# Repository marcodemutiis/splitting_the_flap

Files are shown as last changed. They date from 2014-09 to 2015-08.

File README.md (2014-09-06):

splitting_the_flap
==================

modular split-flap units

splitting the flap is a modular split flap display system based on Arduino. Split flap displays were invented by Solari di Udine in the 60's and used in several train stations and airports around the world. Now out of production and on the path to extinction, I have tried to be as close as possible to the original iconic design.

Project is currently at prototyping stage and files are under constant development - use at your own risk.
stage 0: https://www.youtube.com/watch?v=zjAqb3puniw

All fabrication, circuit and code files are released under MIT license.

For any question, please contact me at: me [at] marcodemutiis.com

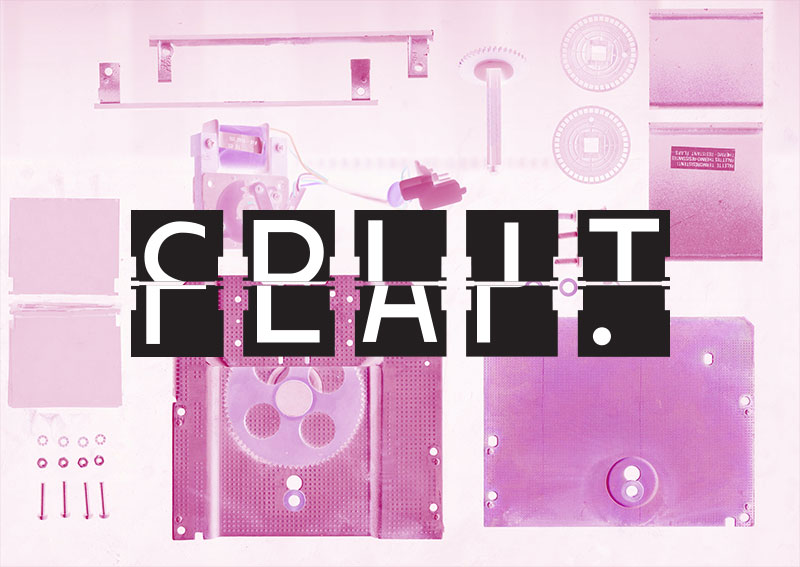
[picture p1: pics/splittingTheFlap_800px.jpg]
splitting_the_flap


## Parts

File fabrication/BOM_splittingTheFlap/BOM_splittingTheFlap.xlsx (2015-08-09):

splitting the flap
Bill of materials (per unit)
PART | NAME | quantity | link | price/unit | price/total
motor | 39步进电机驱动器 39BYG小型电机 20MM机身 0.4A 8N.CM 两相四线 | 1 | http://world.taobao.com/item/17026801379.htm?fromSite=main&spm=a1z09.2.9.60.DnxNuo&_u=91qs2dec14e4
screws | 尼龙/塑料六角螺母 塑胶螺丝螺帽 M2-2.5-3-4-5-6-8-10-12(50颗) [交易快照] 颜色分类: M2.0 白
screws | 颜色分类: M2.0 圆头十字尼龙螺丝 元机尼龙螺钉 塑料螺丝 塑胶螺丝 M2 [交易快照] 颜色分类: m2*12
nylon screws and holders |  |  | https://tengluowujin.world.tmall.com/shop/view_shop.htm?user_number_id=1099047830
acrylic 2.8mm transparent
acrylic 3mm transparent
acrylic 2mm black
acrylic 4mm transparent
EasyDriver |  | 1 | http://world.taobao.com/item/38230922222.htm?fromSite=main&spm=a1z09.2.9.46.DnxNuo&_u=91qs2dec0f0e
rj45 connector (ethernet) | RJ45插座 90度卧式 网络插座 网口母座 56-8P8C全塑 L=17.8mm [交易快照] | 1 | https://klmsm.world.tmall.com/shop/view_shop.htm?spm=a1z09.2.9.160.bYsZt7&user_number_id=1743088708
jumper wires F-F (hall sensor connectors) | 40P杜邦线 双头1P胶壳 总长21CM 12股铜丝 彩排线 40根一排 | 1 | http://world.taobao.com/item/2834445432.htm?fromSite=main&spm=a1z09.2.9.47.s9rnjw&_u=91qs2decbf6f
headers male straight
headers female straight
headers 90 degree male
PVC
PVC silkscreen | 收藏 分享复制链接 举报 透明PVC片丝印 磨砂PVC丝印 面板PVC标贴印刷 服装吊牌标签 |  | http://world.taobao.com/item/38409216170.htm?fromSite=main&spm=a1z09.2.9.230.DnxNuo&_u=91qs2dec7a66
PVC mould cutting |  |  | http://world.taobao.com/item/38409216170.htm?fromSite=main&spm=a1z09.2.9.230.DnxNuo&_u=91qs2dec7a66
acrylic lasercutting |  |  | https://item.taobao.com/item.htm?spm=a1z09.2.9.13.DnxNuo&id=20099696260&_u=91qs2dec31db
ethernet cables | AMPCOM安普康成品六类网线 纯铜CAT6扁平跳线 1/2/3/5/8/10/15米 [交易快照] 颜色分类: 2米无氧铜千兆速率) | 1 | https://ampcom.world.tmall.com/shop/view_shop.htm?spm=a1z09.2.9.183.y7qHXO&user_number_id=2024267815
hall sensors | OH090U(TT ELECTRONICS/OPTEK TECHNOLOGY)[全新原装] | 1 | http://world.taobao.com/item/42828434479.htm?fromSite=main&spm=a1z09.2.9.78.1xjDX0&_u=91qs2deca021
magnets | 稀土永磁王 钕铁硼超强磁钢 永磁铁 白板 方形强力吸铁石4*4*2MM [交易快照] | 1 | https://magpanda.world.tmall.com/shop/view_shop.htm?user_number_id=379092803
PCB print | （冲5钻优惠）3-4天发货 PCB加工 打样 双面板制作5*5 45元10片 | 1 | http://world.taobao.com/item/13063584813.htm?fromSite=main&spm=a1z09.2.9.244.DnxNuo&_u=91qs2dec15ce
resistor
Bill of material (per arduino mega shield)
PCB | （冲5钻优惠）3-4天发货 PCB加工 打样 双面板制作5*5 45元10片 | 1 | http://world.taobao.com/item/13063584813.htm?fromSite=main&spm=a1z09.2.9.244.DnxNuo&_u=91qs2dec15ce
RJ45 Ethernet | RJ45插座 90度卧式 网络插座 网口母座 56-8P8C全塑 L=17.8mm [交易快照] | 14
relay | Arduino Relay 5V/10A单路继电器模块 1路 电磁继电器 高电平驱动 | 1 | http://world.taobao.com/item/18438698638.htm?fromSite=main&spm=a1z09.2.9.161.1xjDX0&_u=91qs2dec5a76

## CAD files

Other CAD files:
fabrication/acrylic/2.8mm/2_8mm.dwg
fabrication/acrylic/2mm/2mm.dwg
fabrication/acrylic/3mm/3mm.dwg
fabrication/acrylic/4mm/4mm.dwg

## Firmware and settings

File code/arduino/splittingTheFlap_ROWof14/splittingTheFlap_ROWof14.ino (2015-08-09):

//////////////////////////////////////////////////////
//stepper connection to Easy Driver 
//red to A left
//blue to A right
//black to B left
//green to B right
//////////////////////////////////////////////////////

#include <AccelStepper.h>

//relay/////////::::::::::::::::::::::::::::::::::::::::::::::::::::::::::::::relay
int relayPin = 53;
//::::::::::::::::::::::::::::::::::::::::::::::::::::::::::::::::::::::::::::::

//I2C communication setup::::::::::::::::::::::::::::::::::::::::::::::::::::::I2C
int deviceID = 1; // 1 = master
int targetDevice = 2; //2-7
int targetCalibDevice = 2; //2-7
int charCounter = 1;
//:::::::::::::::::::::::::::::::::::::::::::::::::::::::::::::::::::::::::::::

//accel stepper and easy driver - motor initialization::::::::::::::::::::::::motor
const int dirPin[] = { 
  9, 12, 4, 14, 38, 44, 50, 29, 23, 26, 32, 35, 41, 47}; //direction pins
const int stepPin[] = { 
  8, 11, 5, 2, 36, 42, 48, 31, 25, 24, 30, 37, 43, 49};//step pins
//init steppers
AccelStepper stepper1(1, stepPin[0], dirPin[0]);
AccelStepper stepper2(1, stepPin[1], dirPin[1]);
AccelStepper stepper3(1, stepPin[2], dirPin[2]);
AccelStepper stepper4(1, stepPin[3], dirPin[3]);
AccelStepper stepper5(1, stepPin[4], dirPin[4]);
AccelStepper stepper6(1, stepPin[5], dirPin[5]);
AccelStepper stepper7(1, stepPin[6], dirPin[6]);
AccelStepper stepper8(1, stepPin[7], dirPin[7]);
AccelStepper stepper9(1, stepPin[8], dirPin[8]);
AccelStepper stepper10(1, stepPin[9], dirPin[9]);
AccelStepper stepper11(1, stepPin[10], dirPin[10]);
AccelStepper stepper12(1, stepPin[11], dirPin[11]);
AccelStepper stepper13(1, stepPin[12], dirPin[12]);
AccelStepper stepper14(1, stepPin[13], dirPin[13]);

AccelStepper allSteppers[] = {
  stepper1, stepper2, stepper3, stepper4, stepper5, stepper6, stepper7, stepper8, stepper9, stepper10, stepper11, stepper12, stepper13, stepper14};

const int totalSteppers = 14;//(sizeof(allSteppers)/sizeof(AccelStepper));
int stepperIndex = 0;
int enblPin[totalSteppers] = {
  7, 10, 6, 3, 34, 40, 46, 33, 27, 22, 28, 39, 45, 51};//enable pins
//:::::::::::::::::::::::::::::::::::::::::::::::::::::::::::::::::::::::::::::

//:::::::::::::::::::::::::::::::::::::::::::::::::::::::::::::::::::::::::::::status
boolean calibrating = false;         // bool for calibartion of each motor
boolean writing = false;             // bool for checking if the whole display is done writing and can accept new string
boolean calibrationRequest = false;  // check if arduino local calibration is do
//:::::::::::::::::::::::::::::::::::::::::::::::::::::::::::::::::::::::::::::

//positioning and flap speed:::::::::::::::::::::::::::::::::::::::::::::::::::pos&speed
int tot = 40;
int howManySteps[totalSteppers];
int lastPos[totalSteppers];
int mySpeed = 3000; //safe < 10000
int myCalibSpeed = 5000;
//:::::::::::::::::::::::::::::::::::::::::::::::::::::::::::::::::::::::::::::

//incoming characters, string handling and splitting:::::::::::::::::::::::::::inBytes
char letters[40] = { 
  '1', '2', '3', '4', '5', '6', '7', '8', '9', '0', 'a', 'b', 'c', 'd', 'e', 'f', 'g', 'h', 'i', 'j', 'k', 'l', 'm', 'n', 'o', 'p', 'q', 'r', 's', 't', 'u', 'v', 'w', 'x', 'y', 'z', '#', '.', '/', ' '   
}; //allowed chars
char inByte;
//char incomingSentence[totalSteppers];
boolean allMotorsStopped = true;
int motorsStopped = 0;

//string handling
int sentenceLength = totalSteppers;       // 14 chars per row
char incomingSentence[totalSteppers];     // a string to hold incoming data
//int stepperIndex;                       // an int to add chars inside the sentence and check amount of chars once the sentence is complete (sentence is complete when it receives '/n' as last char)
boolean startSentence = false;            // whether we can start storing the chars of our sentence (chars start being stored only if first char is a '*')
boolean stringComplete = false;           // whether the string is complete
String inputString = "";                  // a string to hold incoming data

//:::::::::::::::::::::::::::::::::::::::::::::::::::::::::::::::::::::::::::::

//calibration setup::::::::::::::::::::::::::::::::::::::::::::::::::::::::::::calib
const int hallPins[] = { 
  A6, A5, A4, A3, A0, A1, A2, A7, A8, A9, A10, A11, A12, A13};//hall effect pins for calibration
boolean calib[totalSteppers];   //boolean array to store the info on which more motor needs calibration
int calibLast;                  //variable to store the number of the motor that gets calibrated last so we know when calibration is finished
int hallVal[totalSteppers];     //hall effect sensor variables
int hallValPrev[totalSteppers];
int hallThreshold = 500;
//smoothing
const int numReadings = 10;     // how many readings 10
int readings[numReadings];      // the readings from the analog input
int index = 0;                  // the index of the current reading
int total = 0;                  // the running total
int average = 0;                // the average
//:::::::::::::::::::::::::::::::::::::::::::::::::::::::::::::::::::::::::::::

//timer variables to turn off motors:::::::::::::::::::::::::::::::::::::::::::timer
unsigned long currentMillis;
boolean sleep[totalSteppers];              // a bool to check if the motor is off or not
long previousMillis[totalSteppers];        // will store last time timer was set
long interval = 100;                       // interval after which we turn off motor
//calibTimer
unsigned long calibCurrentMillis[totalSteppers];
long calibPreviousMillis[totalSteppers];   // will store last time timer was set
long calibInterval = 5000;                 // interval after which we skip calib

//:::::::::::::::::::::::::::::::::::::::::::::::::::::::::::::::::::::::::::::

////////////////////////////////////////////////////////////////////////////////////////////setup//setuo//setup//setup//setup
void setup(){
  Serial.begin(9600);                       // init Serial

  for(int i = 0; i < totalSteppers; i++){

    pinMode(enblPin[i], OUTPUT);           //init enable pin as outputs
    digitalWrite(enblPin[i], HIGH);        // set enable pin high to turn off motors
    //init motors
    allSteppers[i].setMaxSpeed(mySpeed);
    allSteppers[i].setCurrentPosition(0);
    allSteppers[i].setSpeed(mySpeed);
    lastPos[i] = 39;

    sleep[i] = true;
    previousMillis[i] = 0;

    //calib timer variables
    calibCurrentMillis[i] = 0;
    calibPreviousMillis[i]=0;

    calib[i] = false;
    hallVal[i] = 0;
  }  
  //smoothing
  for (int thisReading = 0; thisReading < numReadings; thisReading++){ //reset average calibration readings
    readings[thisReading] = 0;   
  }
  //string
  inputString.reserve(sentenceLength);                // reserve 98 bytes for the inputString:

  ///relay
  pinMode(relayPin, OUTPUT); //init enable pin as outputs
  powerOFF();

}
/////////////////////////////////////////////////////////////////////////////////////////////loop//loop/loop//loop//loop//loop
void loop(){
  currentMillis = millis(); //update millis counter for timer function  

  //calib start//::::::::::::::::::::::::::::::::::::::::::::::::::::::::::::::::::::::::::::::::::::::::::::::::::::::::::::::::::::://calib start// 
  if(inByte == '='){   //if the incoming char is not an available letter and it is a '=' trigger the calibration function

    Serial.println("calibration begins"); 
    allMotorsStopped = false;  
    powerON();//turn on the relay
    calibrationRequest = true;

    for(int needCalib = 0; needCalib < totalSteppers; needCalib++){    //run through all motors
     
     /* Serial.print("motor #");
      Serial.print(needCalib);
      Serial.print(" hall effect reading = ");
      Serial.println(analogRead(hallPins[needCalib]));*/

      if(analogRead(hallPins[needCalib]) > hallThreshold){             // if the hall effect sensor detects that it is far from magnet, means we are not at zero position

        hallValPrev[needCalib] = analogRead(hallPins[needCalib]) + 1;  
        calib[needCalib] = true;                                       //turn on the needCalib boolean for the motors which need to be calibrated
        calibrating = true;
        calibLast = needCalib;

      }
      else{
        calib[needCalib] = false;                                      //if the hall effect senses that is close to the magnet we are in 0 position, so we turn off the needCalib boolean for the motors (does not need to be calibrated)
      } 
      stepperIndex=0;                                                  //reset stepperIndex
      
    }
  }
  //calib ends//:::::::::::::::::::::::::::::::::::::::::::::::::::::::::::::::::::::::::::::::::::::::::::::::::::::::::::::::::::::://calib ends// 


  //string complete start///::::::::::::::::::::::::::::::::::::::::::::::::::::::::::::::::::::::::::::::::::::::::::::::::::::::::::::::::::::://string complete starts// 
  if (stringComplete && stepperIndex >= sentenceLength) {
Serial.println("writing begins");
    writing = true;
    powerON();//turn on the relay

    allMotorsStopped = false;                        //we switch this boolean in any case just say we got a new string coming in

    for(int i = 0; i < totalSteppers; i++){          //send each char to each stepper 
      for(int newPos = 0; newPos < tot; newPos++){   //run through all the available characters DUPLICATE filter???---------------------
        if( incomingSentence[i] == letters[newPos]){ //and if the incoming char is one of the available characters---------------------
          if(lastPos[i] != newPos){                  //if new letter is different from current letter
            resetTimer(i);                           //reset timer
            if(sleep[i]) {
              wakeUp(i);                             //turn on motor if it was off
            }  
            
            //calculate how many steps to new position////////////
            if (lastPos[i] < newPos) howManySteps[i] = newPos - lastPos[i]; 
            else howManySteps[i] = tot - (lastPos[i] - newPos);
            /////////////////////////////////////////////////////
            allSteppers[i].moveTo(160*howManySteps[i]);  //160. = 1/10 of the motor gear = 1/40 of the flap gear
            allSteppers[i].setSpeed(mySpeed);
            /////////////////////////////////////////////////////
            lastPos[i] = newPos;
          }
        }              
      }
    }
    stepperIndex = 0; //reset stepperIndex
  }
  //string complete ends//::::::::::::::::::::::::::::::::::::::::::::::::::::::::::::::::::::::::::::::::::::::::::::::::::::::::::::::::::::://string complete ends// 


  for(int i = 0; i < totalSteppers; i++){

    if(calib[i] == true) {
      calibrate(i);
    }
  }

  //////////////////////////////////////

  for(int i =0; i < totalSteppers; i++){

    if(allSteppers[i].distanceToGo() == 0){            //if this motor has reached destination

      if(!sleep[i]){
        if(currentMillis - previousMillis[i] > interval){ //if the motor hasnt moved in more than 100 ms
          resetTimer(i); //reset the timer
          goToSleep(i);  //turn off the motor
        }
      }

      allSteppers[i].setCurrentPosition(0);            //set the position to 0

        if(allMotorsStopped == false){
        motorsStopped++;
      }                                 //add the motor to the count of motors that have reached destionation and have been turned off
    }

    else{                                              //if this motor has NOT reached destination
      resetTimer(i);                                   //reset the timer if motor is still running (so it doesn't trigger the timer that turns it off)
      motorsStopped = 0;                                //reset the count of motors that have stopped
      allMotorsStopped = false; 

      allSteppers[i].runSpeedToPosition();             //tell the motor to RUN to position (unless it has reached pos 0)
    }

    if(motorsStopped == totalSteppers){
      allMotorsStopped = true;
      charCounter=0;
      Serial.println("all motors have stopped");

      motorsStopped = totalSteppers+1;
      powerOFF();
      writing = false;
    }
  }
}

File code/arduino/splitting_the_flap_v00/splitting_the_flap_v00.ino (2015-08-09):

/*

  SPLITTING THE FLAP - version 00

  created by Marco De Mutiis 
  2012 - 2014
  more info: www.marcodemutiis.com

*/

//////////////////////////////////////////////////////
//stepper connection to Easy Driver 
//red to A left
//blue to A right
//black to B left
//green to B right
//////////////////////////////////////////////////////

//connections to the Easy Driver
#define DIR_PIN 2      //direction pin 
#define STEP_PIN 3     //step pin
//#define SLEEP_PIN 9
#define ENABLE_PIN 12  //enable pin


char inByte;

//timer variables to turn off the motor if it doesn't move for more than 30 seconds
boolean sleep = true;
unsigned long currentMillis;
long previousMillis = 0;        // will store last time LED was updated
long interval = 30000;           // interval at which to blink (milliseconds)


int tot = 40;
int howManySteps;
int lastPos = 39;

//:::::::::::::::::::::::::::::::::::::::::::::::::::::::::::::::::::::::::::::::::::::::::::::::::::::::::::::::::::::::::::::::::::::::::::: SETUP
void setup() { 
  pinMode(DIR_PIN, OUTPUT); 
  pinMode(STEP_PIN, OUTPUT);
  //pinMode(SLEEP_PIN, OUTPUT); 
  pinMode(ENABLE_PIN, OUTPUT); 

  //digitalWrite(SLEEP_PIN, LOW);
  digitalWrite(ENABLE_PIN, HIGH); //disable all pins of A397 chip
  
  Serial.begin(9600);
} 

//:::::::::::::::::::::::::::::::::::::::::::::::::::::::::::::::::::::::::::::::::::::::::::::::::::::::::::::::::::::::::::::::::::::::::::: LOOP
void loop(){ 

  currentMillis = millis();

  if(Serial.available() > 0){

    inByte = Serial.read(); //store incoming char


    char letters[40] = { 
      '1', '2', '3', '4', '5', '6', '7', '8', '9', '0', 'a', 'b', 'c', 'd', 'e', 'f', 'g', 'h', 'i', 'j', 'k', 'l', 'm', 'n', 'o', 'p', 'q', 'r', 's', 't', 'u', 'v', 'w', 'x', 'y', 'z', '.', '-', '/', ' '   
    };

    for(int newPos =0; newPos<tot; newPos++){
      if(inByte == letters[newPos]){

        //if new letter is different from current letter
        if(lastPos != newPos){ 

          //-----------------------------resetTimer
          resetTimer();
          //-----------------------------wakeUp
          if(sleep) wakeUp();

          //calulate how many steps to new position////////////
          if (lastPos < newPos) howManySteps = newPos - lastPos; 
          else howManySteps = tot - (lastPos - newPos);
          /////////////////////////////////////////////////////


          //print info to monitor///////////////////////////////
          Serial.print("NewPos = ");
          Serial.println(newPos);

          Serial.print("lastPos = ");
          Serial.println(lastPos);

          Serial.print("steps = ");
          Serial.println(howManySteps);
          /////////////////////////////////////////////////////


          //motor spins for howManySteps///////////////////////
          for(int stepNext = 0; stepNext < howManySteps; stepNext++){
            rotate(160, 1.);// 160 = 1/10 of a full revolution of the 1st gear = 1/40 of the last gear = 1 split flap character step //1. = MAX SPEED (slower = stronger)
          } 
          /////////////////////////////////////////////////////

          lastPos = newPos; 
        }     
      }

    }

  }


  if(!sleep){
    // digitalWrite(SLEEP_PIN, LOW);
    if(currentMillis - previousMillis > interval) {   //if the motor hasnt moved in more than 30 secs
      //-----------------------------resetTimer
      resetTimer(); 
      //-----------------------------goToSleep
      goToSleep();
    }
  }
  else(Serial.println("zzzz"));
}

//:::::::::::::::::::::::::::::::::::::::::::::::::::::::::::::::::::::::::::::::::::::::::::::::::::::::::::::::::::::::::::::::::::::::::::: ROTATE
void rotate(int steps, float speed){ 
  //rotate a specific number of microsteps (8 microsteps per step) - (negitive for reverse movement)
  //speed is any number from .01 -> 1 with 1 being fastest - Slower is stronger
  int dir = (steps > 0)? HIGH:LOW;
  steps = abs(steps);

  digitalWrite(DIR_PIN,dir); 

  float usDelay = (1/speed) * 70;

  for(int i=0; i < steps; i++){ 
    digitalWrite(STEP_PIN, HIGH); 
    delayMicroseconds(usDelay); 

    digitalWrite(STEP_PIN, LOW); 
    delayMicroseconds(usDelay); 
  } 
} 
//:::::::::::::::::::::::::::::::::::::::::::::::::::::::::::::::::::::::::::::::::::::::::::::::::::::::::::::::::::::::::::::::::::::::::::: RESET TIMER
void resetTimer(){
  previousMillis = currentMillis;  
}
//:::::::::::::::::::::::::::::::::::::::::::::::::::::::::::::::::::::::::::::::::::::::::::::::::::::::::::::::::::::::::::::::::::::::::::: WAKE UP
void wakeUp(){
  //digitalWrite(SLEEP_PIN, HIGH);
  digitalWrite(ENABLE_PIN, LOW);                  // wake up motor
  sleep = false;
}
//:::::::::::::::::::::::::::::::::::::::::::::::::::::::::::::::::::::::::::::::::::::::::::::::::::::::::::::::::::::::::::::::::::::::::::: GO TO SLEEP
void goToSleep(){
  digitalWrite(ENABLE_PIN, HIGH);                 //disable pins and shut down motor
  sleep = true;
}

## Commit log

2015-09-06 "added scans"
    [2_8mm.dwg, 2mm.dwg, 3mm.dwg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]
2015-09-06 added scans
    [splittingTheFlap_Mega2560Shield_PCB1_11228290_contour.gm1, splittingTheFlap_Mega2560Shield_PCB1_11228290_copperBottom.gbl, splittingTheFlap_Mega2560Shield_PCB1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]
2015-09-06 sensor closeup and video added
2015-09-06 added video ref for sensor and motor
2016-03-04 updated circuit files
    [2_8mm.dwg, 2mm.dwg, 3mm.dwg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]
